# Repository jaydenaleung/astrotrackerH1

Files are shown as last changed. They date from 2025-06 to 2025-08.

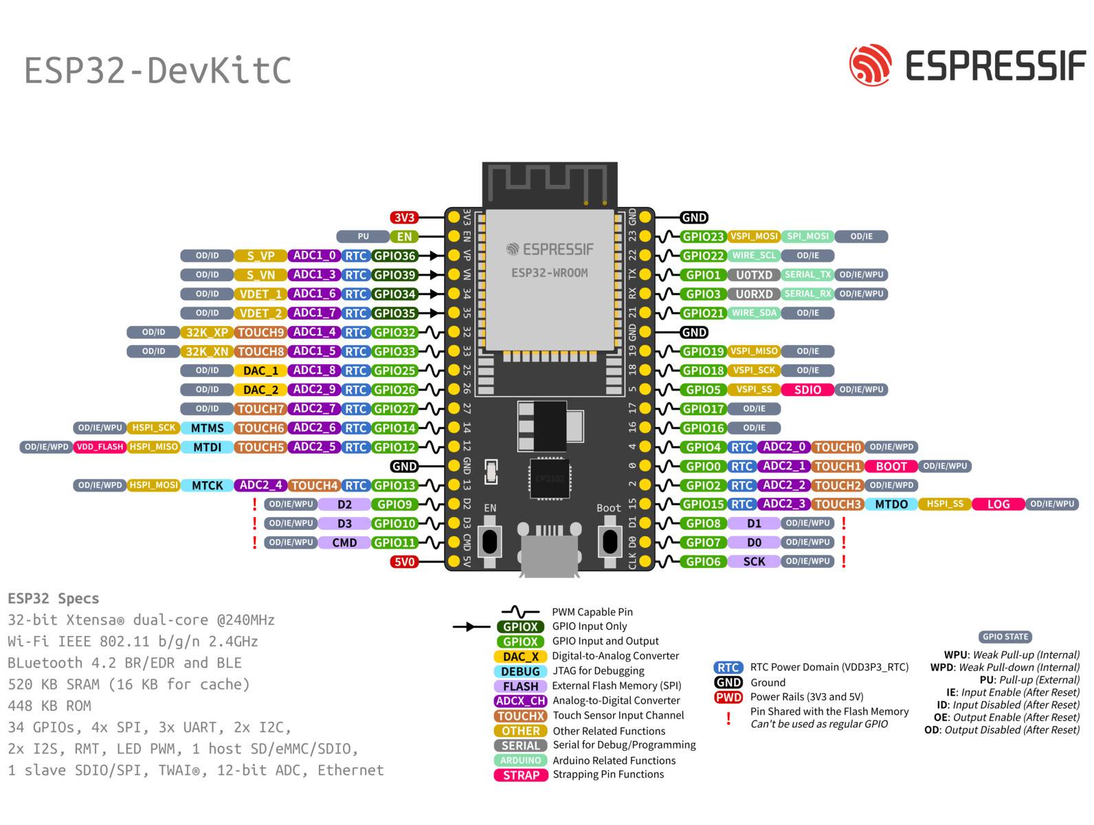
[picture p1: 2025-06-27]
pcb/esp32-pinout.jpg

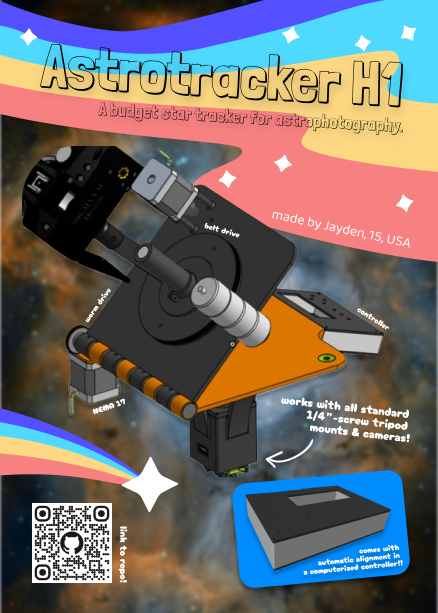
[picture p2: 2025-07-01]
Astrotracker H1 Magazine.png

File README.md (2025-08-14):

# Astrotracker H1
Astrotracker H1 is a DIY star tracker camera mount for astrophotography, made to open access to astrophotography without needing to purchase a more expensive star tracker. Includes a multi-axis rotational gimbal, automatic North Pole alignment, and possible upcoming GoTo integration.

VIDEO DEMO: [https://youtu.be/irbhYrVtJVo](https://youtu.be/irbhYrVtJVo)





# Figures

**Total Minimum Cost:** $220 USD

**Total Hours Spent:** 135 hrs

**Total Days Spent:** 33 days

*See JOURNAL.md and the BOM below for an in-depth explanation of these numbers.*

# How It Works

The Three-Part Process
-

There are always three parts to an engineering project like this, at least for the Highway YSWS program. One is computer-aided design (CAD) modeling; for large projects, this often takes the most time, as it did with this project. Another is printed circuit board (PCB) design, which is the electrical component of the project. Finally, the brain of the build is programmed in the software part, where firmware is written onto a microcontroller that controls the hardware. See the pictures below for how I went about this!

CAD:



PCB:





Firmware:



Star Trackers
-

Since astrophotography is done in very dark environments, a long exposure ranging from a second to the whole night is needed. Due to Earth's rotation, keeping the camera in the same place for a long exposure causes the image to display star trails instead of clear, detailed stars. Star trackers fix this problem by rotating the camera on an equatorial mount aligned with the path of the stars, eliminating star trails. See this picture for a diagrammed explanation:



Astrotracker H1
-

This device attempts to solve these issues by upgrading the traditional equatorial mount to include a polar scope for precise alignment, a counterweight to balance the camera's weight, automatic computerized alignment using azimuthal and latitude (GPS) measurements, and a standard 1/4" tripod mount.

The mechanism is based on two plates connected by a hinge and a rotating gear. The bottom plate is the swivel plate, which swivels 360° and adjusts the azimuthal heading of the device. The other plate is the rotational axis (RA) plate, which tilts to match is angle of elevation to the device's GPS latitude and is driven by a precise worm gear. Matching the device's rotation to face exactly 0° north and its tilt to its GPS latitude allows the RA, the axis perpendicular to and in the middle of the rotating gear and the RA plate, to point exactly to the North Pole (next to the star Polaris). When the RA is pointed toward the North Pole and the rotating gear turns counterclockwise, the tracking will be able to accurately and precisely follow the path of the stars and prevent capturing star trails. Microstepping enhances these features by increasing the precision and resolution of the stepper motor by up to 64 times.



Additional Features
-

Apart from the bare-bones mechanism that drives the star tracker, these upgrades elevate the project to create a truly effective star tracker:
- Automatic, computerized alignment using GPS and compass data
- 1/16 and 1/64 microstepping for stepper motors
- Polar scope for precise adjustment
- Counterweight for balance
- Bubble level for precision
- Thrust and radial ball bearings for smooth rotation
- 12.5:1 reduction ratio for belt-driven rotating gear
- 60:1 reduction ratio for worm gear-driven hinge
- 51:1 reduction ratio for the gearbox on the stepper motor turning the swivel plate
- Organized PCB connecting everything on one board
- Standard 1/4" camera and tripod mount screws
- Ball mount to point camera the right way
- Center control console with up-down-left-right buttons for fine adjustment, start-stop tracking buttons, auto-adjustment capability, and a smart LCD UI interface





# The 'Why' Behind the Project
As an avid photographer and engineer myself, I have always wanted to get more involved with astrophotography. Unfortunately, living in a city didn't play out well for me because of the massive amount of light pollution around me, blocking my view of the stars. I knew I wanted to combine my passions, and the opportunity to do so came through Hack Club's Highway to Undercity program. They fund almost any project you propose to them through their You Ship We Ship (YSWS) initiative.

After conducting some research, I found out that a star tracker was one of the most necessary tools to take better pictures of the night sky. Unfortunately, they were all priced around $500 USD - a hefty investment. Building a star tracker would allow me to combine my passions and achieve a more cost-effective solution at the same time.

# Why This Is Worth Ten Points
This star tracker isn't just any star tracker or equatorial mount - it adds many more complex features that empower young photographers on a budget, like myself, to pursue astrophotography. Fundamentally, the project is already as mechanically complex as a six-point project without all of the additional features. The time spent building intricate features into the mechanical model, custom footprints into the PCB, and special features into the firmware truly takes this project above and beyond the guidelines for a six-point project. 

Not only did I pay attention to the detail and precision needed for such a device with the bubble level, high reduction ratios, and microstepping, but I also considered what would take this above its minimum viable product by adding complex logic for auto-alignment, a balancing counterweight to increase control, and an intuitive LCD user interface controlled with standard pushbuttons. Being able to connect all the electrical components on a single, thought-out PCB and the firmware logic for tracking and auto-alignment indeed also makes this project electrically and computationally complex. Furthermore, I was able to achieve all of these features for under $300 USD when most market star trackers cost about $500 USD. Finally, I spent a ton of time perfecting every detail and feature, putting in almost sixty hours *before* building it (while the recommended minimum time spent for a ten-point project is fifty hours).

# **Bill of Materials (BOM):**

*Note: I am using Aliexpress for some and Amazon for others. Prices listed below are in USD, per part, and rounded. e.g. 2x Nema 17 ($14) = $28 total. Also see the .csv file for the official BOM.*

| Quantity | Name | Price Per Part | Link |
| ----- | --- | --- | --- |
| 2x | Nema 17 stepper motor (regular) | $14 | [https://www.amazon.com/STEPPERONLINE-Stepper-Bipolar-Connector-compatible/dp/B00PNEQKC0](url) |
| 1x | Nema 17 stepper motor (w/gearbox) | $42 | [https://www.amazon.com/51-Planetary-Gearbox-Stepper-Precision/dp/B00QEVLDVO](url) |
| 1x | F8-22M thrust ball bearing | $1 | [https://www.aliexpress.us/item/3256807051413217.html](url) |
| 1x | 10-pack radial ball bearing, 3mm bore | $2 | [https://www.aliexpress.us/item/3256807605344885.html](url) |
| 1x | Worm gear set (worm + gear) | $12 | [https://www.amazon.com/uxcell-Worm-Gear-Set-Reduction/dp/B0DFCVKXLX](url) |
| 1x | PCB board (through JLCPCB & Hack Club $20 Coupon) | $0, covered by coupon | See gerbers.zip in 'pcb' folder |
| 1x | 20-pack 6x6x14 pushbutton | $1 | [https://www.aliexpress.us/item/2255800980685095.html](url) |
| 1x | I2C 16x2 LCD with I2C backpack, blue color | $1 | [https://www.aliexpress.us/item/3256808568663888.html](url) |
| 1x | ESP32 DEVKIT WROOM-32 38-Pin Development Board Type-C | $1 | [https://www.aliexpress.us/item/3256808295104972.html](url) |
| 1x | Resistor pack | $5 | [https://www.amazon.com/Resistor-Resistors-Assortment-Breadboard-Electronics/dp/B0F4P352BB](url) |
| 1x | NEO-8M GPS Module | $1 | [https://www.aliexpress.us/item/3256806859439052.html](url) |
| 1x | QMC5883L Compass Module | $2 | [https://www.aliexpress.us/item/3256807913730129.html](url) |
| 3x | TMC2209 stepper motor driver | $1 | [https://www.aliexpress.us/item/3256808046478114.html](url) |
| 1x | 16T 5mm bore gear | $7 | [https://www.amazon.com/WINSINN-Aluminum-Synchronous-Timing-Printer/dp/B077GMR328](url) |
| 1x | 16T toothless idler bearing for 6mm width GT2 belt, 3mm bore | $9 | [https://www.amazon.com/WINSINN-Aluminum-Timing-Toothless-Printer/dp/B07BPHPYTN?th=1](url) |
| 1x | 2-pack GT2 6mm width belt, 530mm length | $7 | [https://www.aliexpress.us/item/3256808983126633.html?gatewayAdapt=glo2usa4itemAdapt](url) |
| 1x | Polar scope | $27 | [https://www.amazon.com/Tydeux-Polar-Telescope-Finderscope-EQ-5/dp/B0D2L11C4G/](url) |
| 1x | 3-pack 1/4" camera screw | $1 | [https://www.aliexpress.us/item/3256806761503223.html](url) |
| 1x | Camera ball joint mount, red color | $1 | [https://www.aliexpress.us/item/3256802805830814.html](url) |
| 1x | 5-pack bubble level, 18x9mm | $1 | [https://www.aliexpress.us/item/3256808611329580.html](url) |
| 4x | 200g counterweight | $1 | [https://www.aliexpress.us/item/3256807217165073.html](url) |
| 1x | 6S LiPo battery, 22.2V 1000mAh 100C, XT60 connector | $15 | [https://www.amazon.com/Ovonic-Battery-1000mAh-Connector-CINEWHOOP/dp/B07JPK99D9](url) |
| 1x | XT60 male and female plug pack wires, 14 AWG, 15cm length | $1 | [https://www.aliexpress.us/item/3256808104814371.html](url) |
| 1x | LiPo battery charger | $30 | [https://www.amazon.com/B6-Battery-Charger-Discharger-Connectors/dp/B0F2H3XR6S](url) |
| 1x | M4 nuts and bolts, 270 pcs | $9 | [https://www.amazon.com/Kadrick-Assortment-Metric-Washers-Upgrade/dp/B0BZ6XG8PT?th=1](url) |
| 4x | M3 50pcs bolts, 6mm, 12mm, 16mm, 35mm versions | $1 | [https://www.aliexpress.us/item/2255800794906149.html](url) |
| 1x | M3 50 pcs hex nuts | $1 | [https://www.aliexpress.us/item/3256807407546447.html](url) |
| 1x | M2.5x30mm 50pcs bolts | $1 | [https://www.aliexpress.us/item/2255799955713291.html](url) |
| 1x | M2.5 50 pcs nuts | $1 | [https://www.aliexpress.us/item/3256807407546447.html](url) |
| 1x | Allen key set | $1 | [https://www.aliexpress.us/item/3256807283413035.html](url) |
| 1x | Long-nosed plier | $1 | [https://www.aliexpress.us/item/3256805792649837.html](url) |

| **Total minimum cost** | $220 |
| --- | ----- |
| **Total including 'in-case' of price changes, spare parts, etc.** | ~$235 |
| **Total including in-cases, sales tax (assumed ~6%), import and customs fees, etc.** | ~$270 |

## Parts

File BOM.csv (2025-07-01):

Quantity | Name | Price Per Part | Link
2x | Nema 17 stepper motor (regular) | $14 | https://www.amazon.com/STEPPERONLINE-Stepper-Bipolar-Connector-compatible/dp/B00PNEQKC0
1x | Nema 17 stepper motor (w/gearbox) | $42 | https://www.amazon.com/51-Planetary-Gearbox-Stepper-Precision/dp/B00QEVLDVO
1x | F8-22M thrust ball bearing | $1 | https://www.aliexpress.us/item/3256807051413217.html
1x | 10-pack radial ball bearing 3mm bore | $2 | https://www.aliexpress.us/item/3256807605344885.html
1x | Worm gear set (worm + gear) | $12 | https://www.amazon.com/uxcell-Worm-Gear-Set-Reduction/dp/B0DFCVKXLX
1x | PCB board (through JLCPCB & Hack Club $20 Coupon) | $0 - covered by coupon | See gerbers.zip in 'pcb' folder
1x | 20-pack 6x6x14 pushbutton | $1 | https://www.aliexpress.us/item/2255800980685095.html
1x | I2C 16x2 LCD with I2C backpack blue color | $1 | https://www.aliexpress.us/item/3256808568663888.html
1x | ESP32 DEVKIT WROOM-32 38-Pin Development Board Type-C | $1 | https://www.aliexpress.us/item/3256808295104972.html
1x | Resistor pack | $5 | https://www.amazon.com/Resistor-Resistors-Assortment-Breadboard-Electronics/dp/B0F4P352BB
1x | NEO-8M GPS Module | $1 | https://www.aliexpress.us/item/3256806859439052.html
1x | QMC5883L Compass Module | $2 | https://www.aliexpress.us/item/3256807913730129.html
3x | TMC2209 stepper motor driver | $1 | https://www.aliexpress.us/item/3256808046478114.html
1x | 16T 5mm bore gear | $7 | https://www.amazon.com/WINSINN-Aluminum-Synchronous-Timing-Printer/dp/B077GMR328
1x | 16T toothless idler bearing for 6mm width GT2 belt 3mm bore | $9 | https://www.amazon.com/WINSINN-Aluminum-Timing-Toothless-Printer/dp/B07BPHPYTN?th=1
1x | 2-pack GT2 6mm width belt 530mm length | $7 | https://www.aliexpress.us/item/3256808983126633.html?gatewayAdapt=glo2usa4itemAdapt
1x | Polar scope | $27 | https://www.amazon.com/Tydeux-Polar-Telescope-Finderscope-EQ-5/dp/B0D2L11C4G/
1x | 3-pack 1/4 inch camera screw | $1 | https://www.aliexpress.us/item/3256806761503223.html
1x | Camera ball joint mount red color | $1 | https://www.aliexpress.us/item/3256802805830814.html
1x | 5-pack bubble level 18x9mm | $1 | https://www.aliexpress.us/item/3256808611329580.html
4x | 200g counterweight | $1 | https://www.aliexpress.us/item/3256807217165073.html
1x | 6S LiPo battery 22.2V 1000mAh 100C XT60 connector | $15 | https://www.amazon.com/Ovonic-Battery-1000mAh-Connector-CINEWHOOP/dp/B07JPK99D9
1x | XT60 male and female plug pack wires 14 AWG 15cm length | $1 | https://www.aliexpress.us/item/3256808104814371.html
1x | LiPo battery charger | $30 | https://www.amazon.com/B6-Battery-Charger-Discharger-Connectors/dp/B0F2H3XR6S
1x | M4 nuts and bolts 270 pcs | $9 | https://www.amazon.com/Kadrick-Assortment-Metric-Washers-Upgrade/dp/B0BZ6XG8PT?th=1
4x | M3 50pcs bolts 6mm 12mm 16mm 35mm versions | $1 | https://www.aliexpress.us/item/2255800794906149.html
1x | M3 50 pcs hex nuts | $1 | https://www.aliexpress.us/item/3256807407546447.html
1x | M2.5x30mm 50pcs bolts | $1 | https://www.aliexpress.us/item/2255799955713291.html
1x | M2.5 50 pcs nuts | $1 | https://www.aliexpress.us/item/3256807407546447.html
1x | Allen key set | $1 | https://www.aliexpress.us/item/3256807283413035.html
1x | Long-nosed plier | $1 | https://www.aliexpress.us/item/3256805792649837.html
Total minimum cost | $220
Total including 'in-case' of price changes; spare parts; etc. | ~$235
Total including in-cases; sales tax (assumed ~6%); import and customs fees; etc. | ~$270

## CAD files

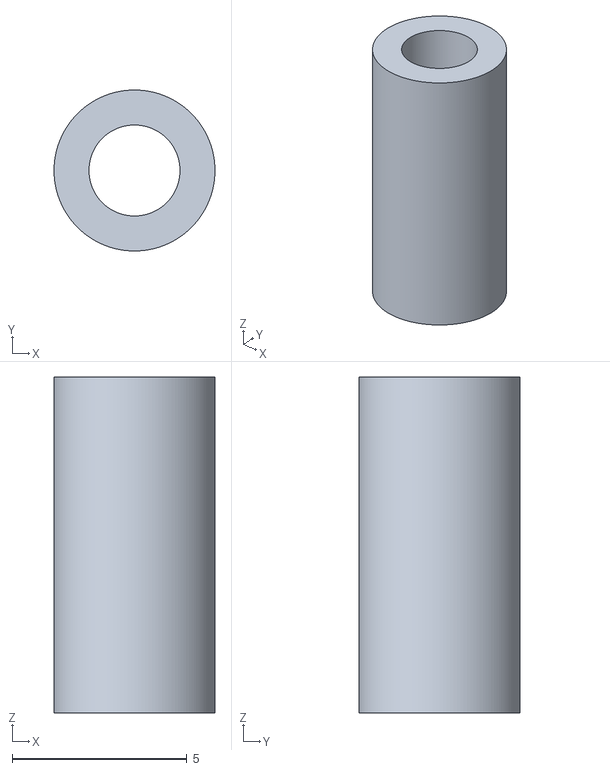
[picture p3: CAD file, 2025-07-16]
cad/parts to print/M2.5x9.6mm spacer - Part 1.stl
4.60 x 4.60 x 9.60

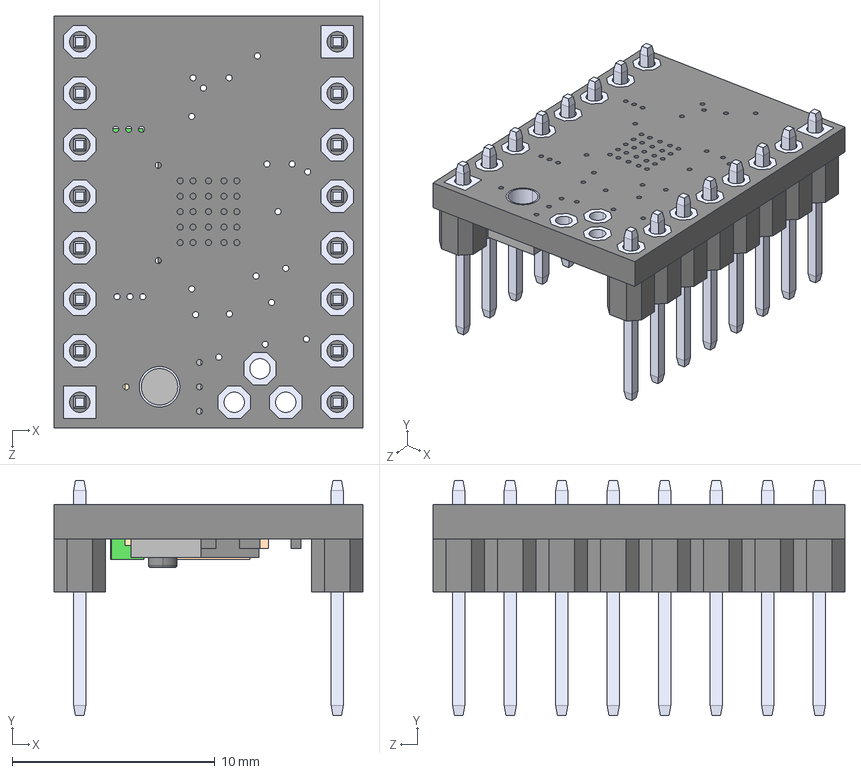
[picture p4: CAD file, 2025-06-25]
cad/reference/TMC2209_SILENTSTEPSTICK.step
15.2 x 11.6 x 20.3 mm

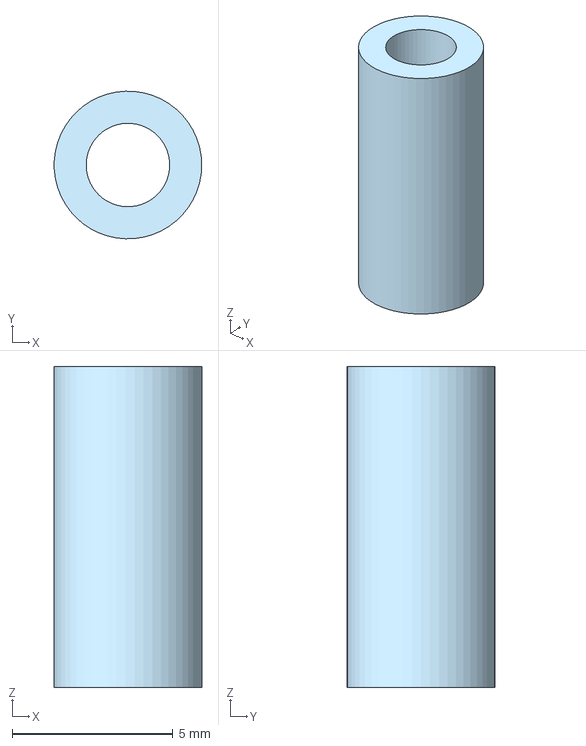
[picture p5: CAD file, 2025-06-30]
cad/spacers/M2.5x10mm spacer.step
4.60 x 4.60 x 10.0 mm

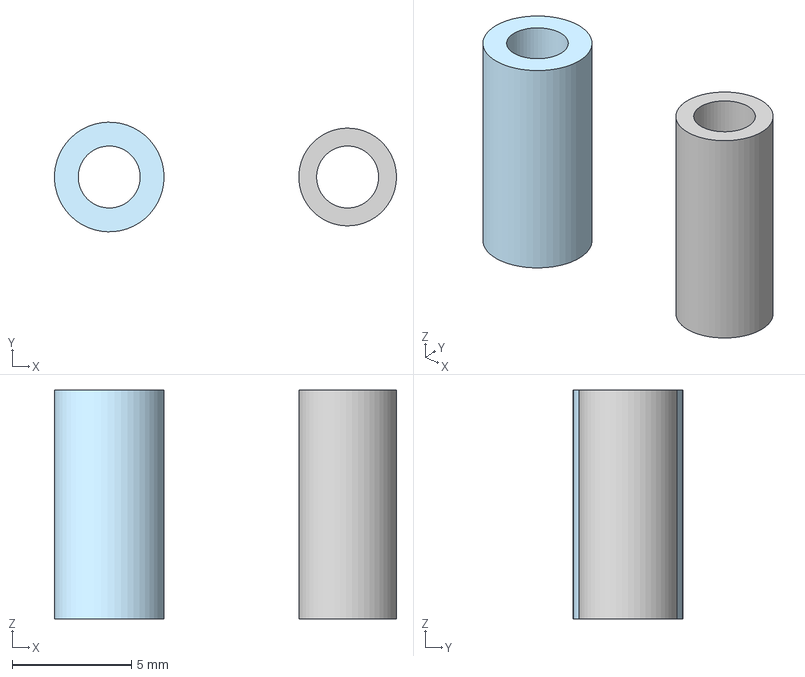
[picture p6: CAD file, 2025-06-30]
cad/spacers/M2.5x9.6mm spacer.step
14.3 x 4.60 x 9.60 mm

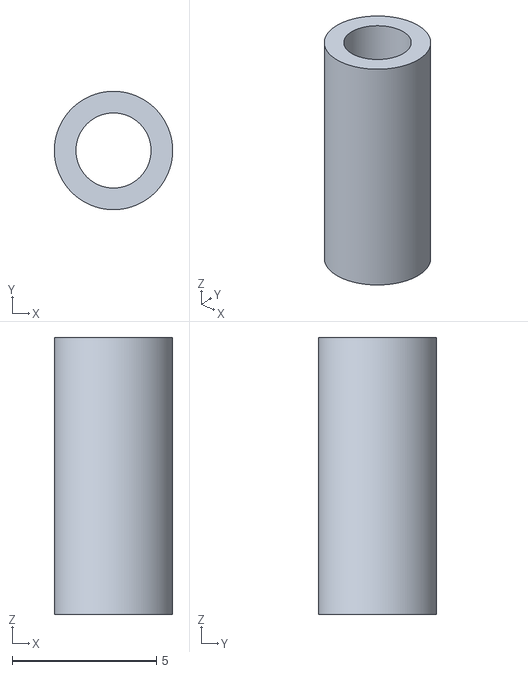
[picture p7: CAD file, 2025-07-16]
cad/parts to print/M2.5x9.6mm spacer - Part 2.stl
4.10 x 4.10 x 9.60

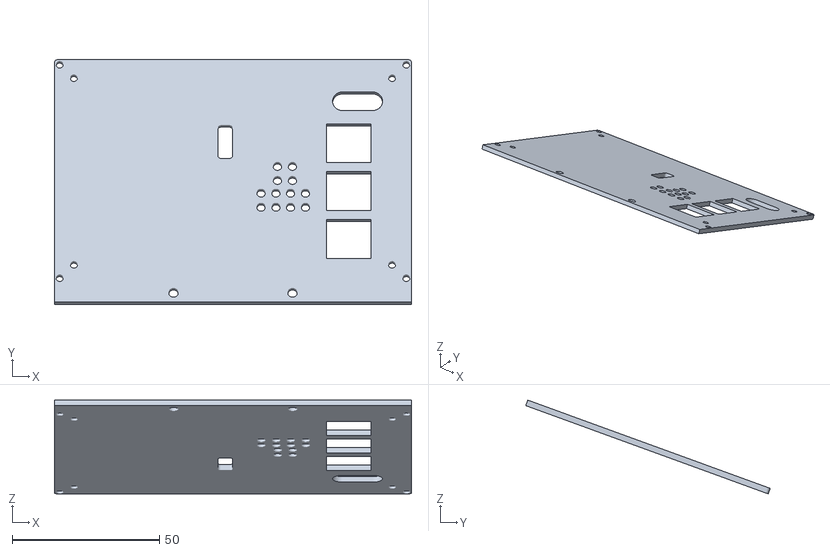
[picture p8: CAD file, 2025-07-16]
cad/parts to print/Swivel Plate - Part 1.stl
121.3 x 83.1 x 31.9

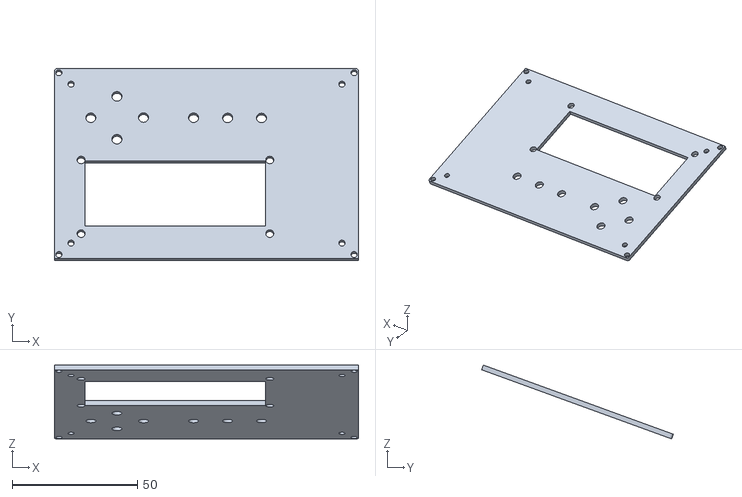
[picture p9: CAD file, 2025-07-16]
cad/parts to print/Swivel Plate - Part 4.stl
121.3 x 76.5 x 29.5

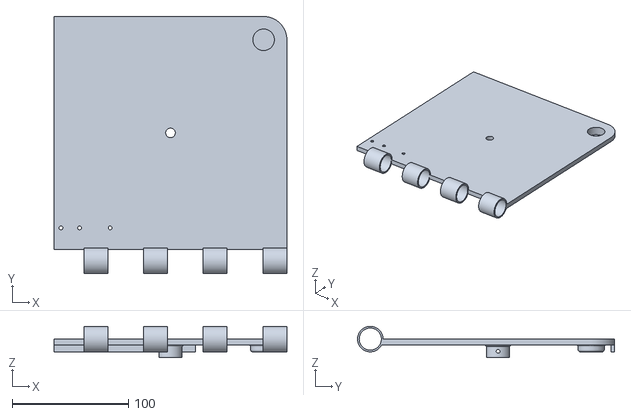
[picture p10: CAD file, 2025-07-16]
cad/parts to print/Swivel Plate - Part 7.stl
200.0 x 220.8 x 27.0

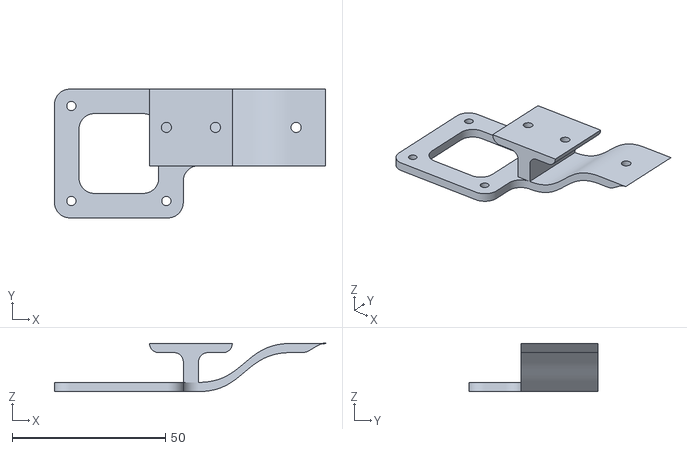
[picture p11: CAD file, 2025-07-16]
cad/parts to print/Swivel Plate - Part 6.stl
88.4 x 42.0 x 15.7

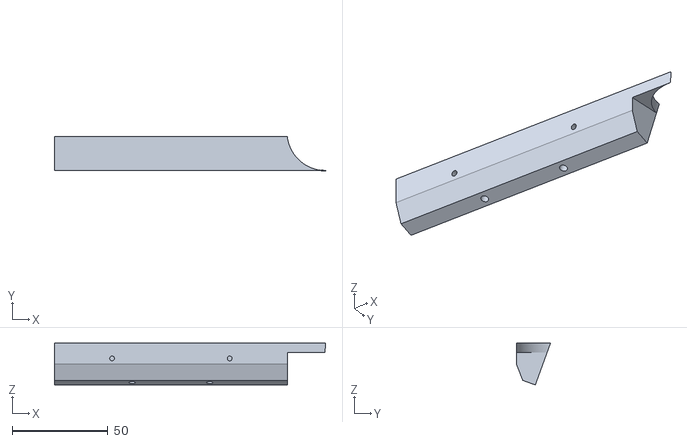
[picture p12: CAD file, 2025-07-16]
cad/parts to print/Swivel Plate - Part 8.stl
141.2 x 17.8 x 21.8

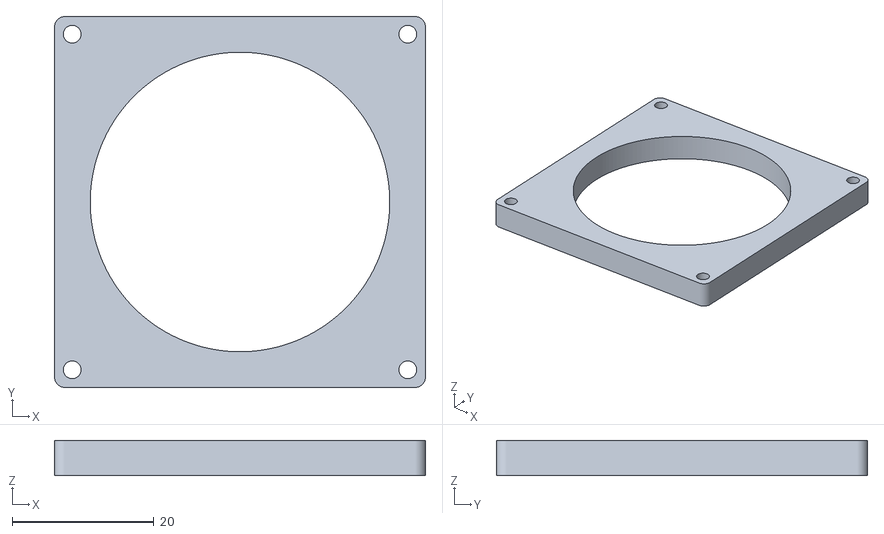
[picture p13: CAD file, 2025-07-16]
cad/parts to print/swivel motor housing - Part 1.stl
52.4 x 52.4 x 5.00

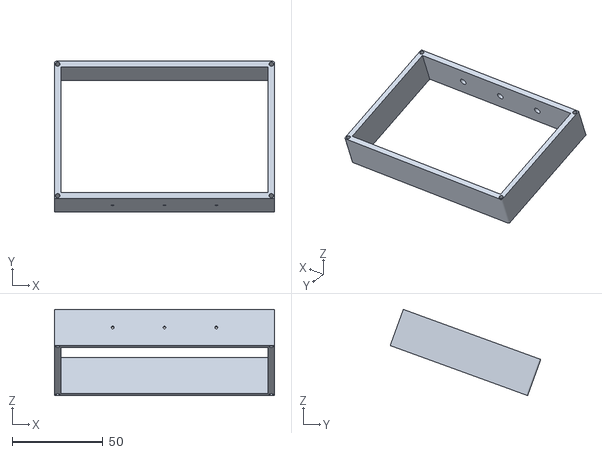
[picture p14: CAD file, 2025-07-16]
cad/parts to print/Swivel Plate - Part 3.stl
121.3 x 83.1 x 47.5

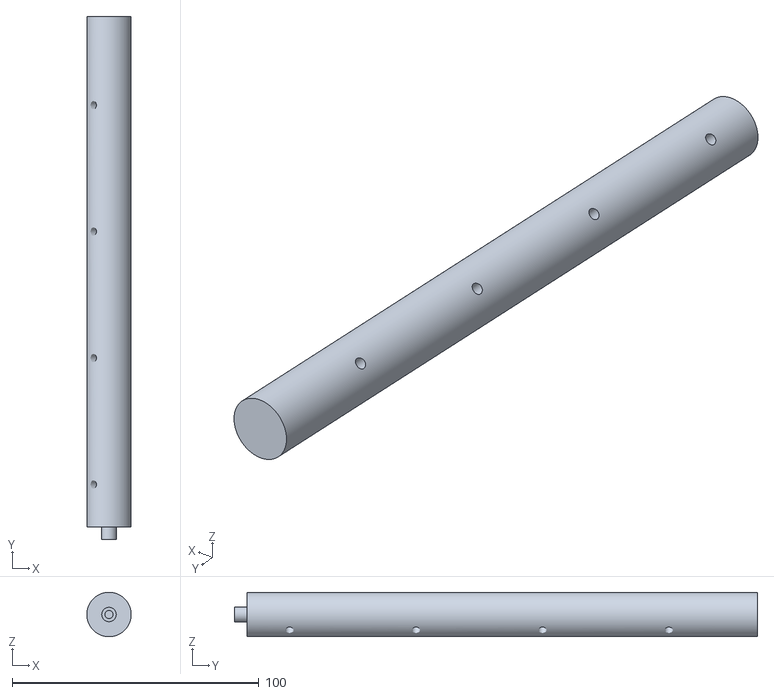
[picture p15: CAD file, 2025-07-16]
cad/parts to print/hinge - Part 1.stl
18.0 x 212.0 x 18.0

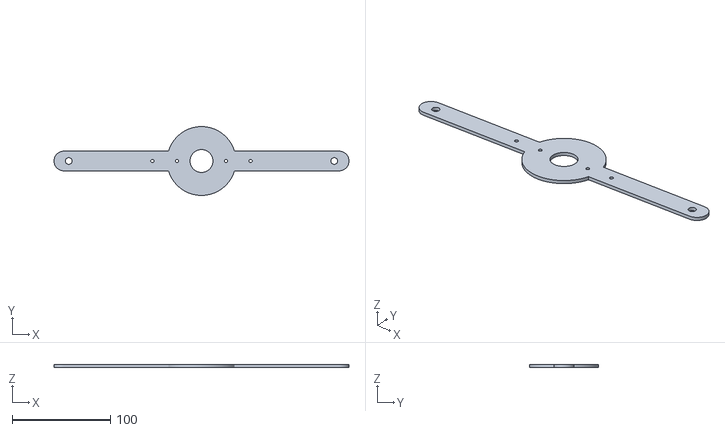
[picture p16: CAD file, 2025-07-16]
cad/parts to print/camera mount - Part 1.stl
300.0 x 70.0 x 3.00

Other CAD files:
cad/parts to print/M2.5x10mm spacer.stl
cad/parts to print/RA Plate - Part 1.stl
cad/parts to print/polar scope circlip - Part 1.stl
cad/parts to print/M4x0.8mm spacer.stl
cad/parts to print/M3x8mm spacer.stl
cad/spacers/M3x8mm spacer.step
cad/spacers/M4x0.8mm spacer.step

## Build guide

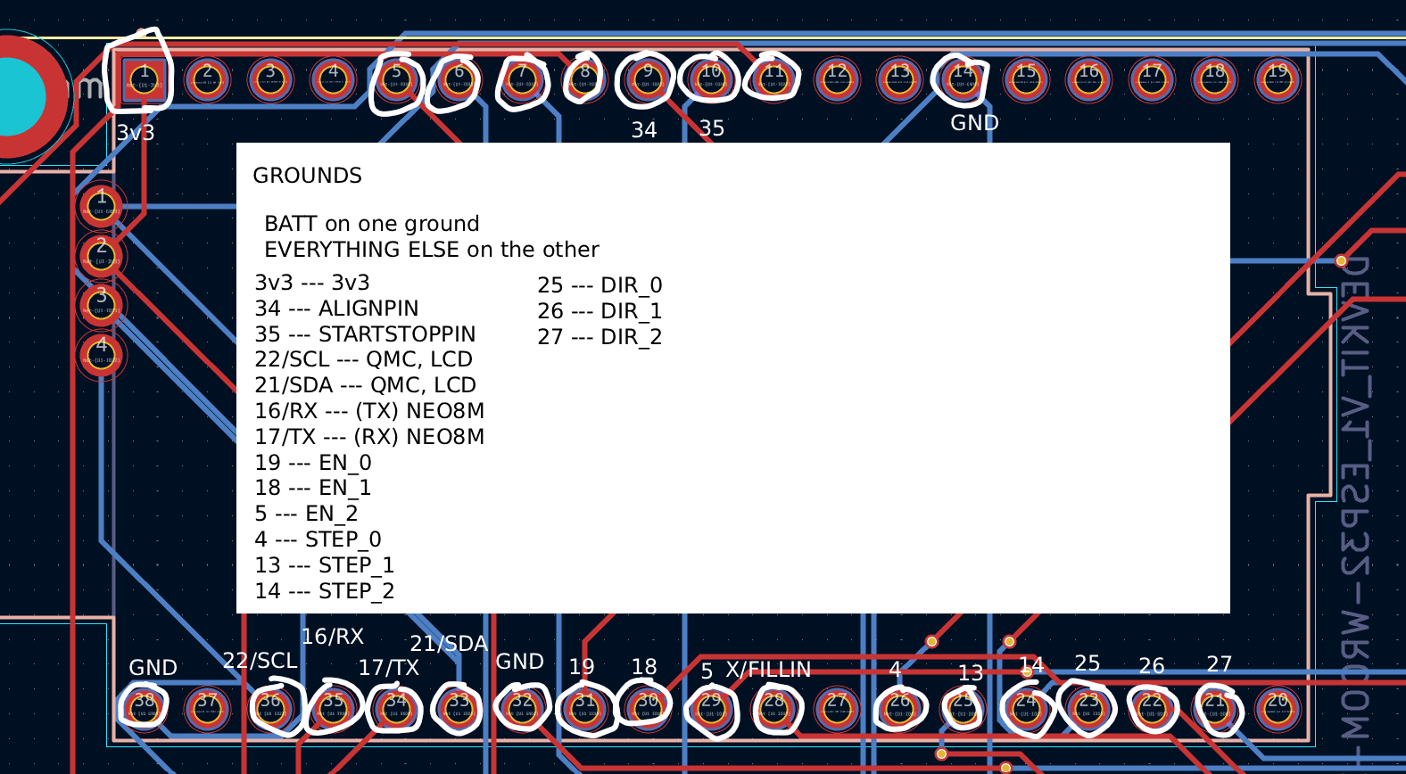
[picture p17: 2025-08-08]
pcb/ESP32 30-Pin Wiring Diagram Translation.png

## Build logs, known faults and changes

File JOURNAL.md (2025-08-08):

---
title: "Astrotracker H1"
author: "Jayden Leung (Hack Club Slack: loliipoppi)"
description: "DIY star tracker for astrophotography with a 360° azimuthal axis, adjustable tilt, and automatic North Pole finding."
created_at: "2025-06-11"
---

# Time Spent
- **Total hours: 135h**
- **Total days: 33 days**
- **Time spent on CAD: 27.5h**
- **Time spent on PCB design: 11h**
- **Time spent on coding: 9h**
- **Time spent on physical assembly: 78h**
- **Time spent on sourcing parts, writing journal and readme, etc.: ~10.5h**

# June 11th: Research and Planning

Before beginning the technical work on my project, I needed to first research how a star tracker worked and what the best design for it was. I learned my lesson in previous projects to do this step first before jumping right in so I can maximize my efficiency. Bottom line, start with your MVP (minimum viable product) and build up instead of shooting for the stars and having to cut down on your project.

ChatGPT was my best friend here. I looked at a few YouTube videos, websites, forums, similar projects, etc., but ChatGPT was able to answer all my questions on simple star movements. Here are some of the resources I used: https://wiki.openastrotech.com/en/OpenAstroTracker, https://openastrotech.com/, https://agenaastro.com/sky-watcher-star-adventurer-gti-goto-mount-head-kit-s20590.html?rfsn=7382628.cf60d1, https://www.youtube.com/watch?v=RtHJ5TVkeu4

Through a series of questions, conclusions, and deductions (see my whiteboard planning below), I found out that, from Earth, stars appear to move east/counterclockwise around Polaris (the north star) at the sidereal rate (~15°/hr). This meant that all I had to do was point the axis of my rotational plate towards Polaris and turn the plate counterclockwise at 15°/hr to match the movement of the stars. It also turned out that this would work no matter the direction the camera was pointed in or even if the camera wasn't centered on the rotational axis, as long as it was physically connected to the rotational plate.



I also sketched a few examples of what the tracker could look like in CAD. I eventually settled on the second iteration (look at the second picture). Sketching first helped me to effectively iterate and create the most efficient design without having to take a lot of time.




This was my MVP in the end (see below). There were a few assumptions and oversights that I intentionally made to simplify the design first.

Functions (Must be able to…):
- Rotate the rotating base
- Have near-270 deg turn for camera
- Align the rotating base

Parts (Must have…):
- Base that rotates the rotating base
- Rotating base - stepper motor
- Mount on rotating base for camera (use tripod mount on the camera)

Restrictions (OK to not have…):
- Belt drive/worm gear & ball bearings
- Tripod mount
- Northern/southern hemisphere switching
- Auto Correction for Polaris/rotating base calibration depending on coords
- GoTo compatibility
- Offset for through-hole polar scope OR polar scope off to the side

**Total time spent: 5h**

# June 12-13th: CADing the Rotational Plate and Hinge

The next two days after planning I spent CADing the rotational plate, swivel plate, and the hinge that connected them in Onshape. I followed the format shown in the second design (look at the previous journal entry). I decided to have the rotational gear (RA gear) be connected to a stepper motor through a belt drive system. This would provide enough torque to move the heavy camera and enable the device to rotate the plate at the slow speed of 15°/hr. I first settled for a 400T RA gear, which would give me a 1:25 gear ratio for a 16T stepper motor gear. With 1.8° steps and 1/32 microstepping (using PWM to split the steps even further on the stepper motor), that would have given me about 8.1 arcseconds/microstep, which was within the optimal range for medium to long range (zoom) astrophotography.

After discovering that a 400T gear was pretty big, I settled for a 200T gear instead but had to increase the 1/32 microstepping to 1/64 to maintain the rotational rate of 8.1 arcsecs/microstep. This would also give me enough torque to move a payload of about 500g-1kg. I ran some calculations and found that the optimal center to center distance between the RA gear and the stepper motor gear was 100mm. This would allow the gears to be close enough to mimize the size of the plate while still allowing enough space between the two gears for idler bearings that would fit the timing belt tighter. 200T gear, 16T gear, and 100mm C-C dist => 530mm GT2 belt; the GT2 belt had a pitch (tooth-to-tooth distance) of 2mm and was a bit long for the setup, but was perfect after securing it with a 20T toothless idler bearing that jutted 3.1mm into the belt.

I CADed this onto the rotational plate (RA plate), which I then connected via a hinge controlled by a worm gear to the swivel plate. The swivel plate would allow the whole mechanism to swivel along the azimuth/horizon, and the worm gear tilted the RA plate towards Polaris (the angle of elevation of the plate should equal my GPS latitude). The RA gear was generated by an Onshape script, and I CADed its additional details by hand since I couldn't find an internet model for a 200T belt drive gear. I found one for the 16T gear, though. See the picture below!

Screenshot 2025-06-16 at 3 56 46 PM

**Total time spent: 5.5h**

# June 16th: CADing the Swivel Plate and Adding Accurate Part Models

I spent today adding the functionality for the swivel plate (the plate that is connected to the RA plate by a hinge) by creating a housing for another NEMA 17 stepper motor with a 51:1 gear reduction gearbox. On top of the motor sits a thrust ball bearing, and on top of that sits the swivel plate and the entire mechanism with it. Next time, when I put the finishing touches on my CAD model, I'll make sure to add arms to the housing that curve up to support the heavy swivel plate; I didn't get to do it this time. This is a crucial part of the device since it rotates the RA plate to face Polaris on the azimuthal axis. However, I do have some reservations about allowing the entire mechanism (possibly ~500g) to sit on top of a ball bearing and a motor housing, especially when considering the extra 1-2kg load put on by the camera and its opposing counterweight. Those changes will have to be determined after printing and testing.

In case you're confused about how I spent five hours on this, I had to first research the best way to effectively rotate the swivel plate, run calculations to find the best motor gearbox that would allow for enough torque, and find the best bearing that would work for this. I also finally decided to spend some time finding online models of the motors and bearings I was using. To my great surprise, downloading the files as STEP files instead of STL files made it SO MUCH EASIER because I was working with solid, editable parts rather than meshes. Onshape was much friendlier to me with these files because of this. I was surprised because I thought I had tried this before with an earlier plane project, and they still were meshes. Meshes or not, this greatly simplified my work as it allowed me to make the right edits to these models to ensure they were accurate to the specific motor dimensions I was working with.

For reference, here are some great websites and libraries of CAD models that were helpfuL: [https://grabcad.com/library](url), [www.traceparts.com/en](url), [https://www.thingiverse.com/](url), (next two are more STLs and 3D printing files, along with Thingiverse) [https://cults3d.com/](url), [https://www.printables.com/](url).

And just as a side note, before I started working on the CAD files, I finally decided to make and update my journal. It took a few hours since I re-read all the custom project rules and had to set up my journal from scratch.

Pictures of the updated assembly!
Screenshot 2025-06-17 at 5 20 49 AM
Screenshot 2025-06-17 at 5 21 13 AM
Screenshot 2025-06-17 at 5 21 43 AM
Screenshot 2025-06-17 at 5 22 08 AM

**Total time spent: 5h**

# June 18-23: Finishing the CAD (for now)

Throughout these six days (I was working quite sporadically, which is why it took so long), I finally finished adding the final touches and reference model to my assembly. It looks great!! I employed a dark grey-orange color scheme to match the color of my tripod.

Before I reveal the final result, I'll list the changes I made:
- Added real models of the NEMA 17 stepper motors
- Created and added housing for the NEMA 17 gearbox that turns the whole mechanism
- Implemented a thrust bearing to make the turning of the mechanism smoother
- Added arms onto the motor housing to better support the heavy mechanism, using ball bearings to reduce friction
- Added compatibility for the polar scope
- Added a mount for the camera and its counterweight
- Added a restraining clip to hold the gear and camera mount down
- Added a bubble/spirit level on the swivel plate for extra accuracy
- Placed ball bearing model into the assembly
- Placed polar scope model into the assembly
- Placed camera, camera mount, counterweight, and 1/4-20 screws for the camera into the assembly
- Placed tripod into the assembly
- Changed colors to dark grey-orange to reflect my tripod
Screenshot 2025-06-23 at 8 30 47 PM

Here are the final results! I'll update the model again after I'm finished with the PCB design, and I'll add a housing for the PCB.
Screenshot 2025-06-23 at 8 30 19 PM
Screenshot 2025-06-23 at 8 30 32 PM
Screenshot 2025-06-23 at 7 49 47 PM

**Total time spent: 9h**

# June 24: PCB Part Sourcing & Schematic

As I got started on my PCB design (which, as I found being a beginner, had a steep learning curve), I quickly ran into trouble sourcing parts, symbols, footprints, and the like. I found [snapeda.com](url) (and surprisingly, no other websites) to be really helpful in this, until I encountered the "No 2D model" (symbol or footprint) label for some parts. These were mostly the parts that weren't as common, such as the QMC5883L compass module I was using, so I had to learn how to make the footprints and symbols by hand. While it was certainly frustrating and time-consuming, I think it was a good exercise, as I heard from people around the internet that that was a common area of PCB design. Here's a good resource I found: [https://www.youtube.com/watch?v=NiSkKemLK_8](url). I had to make "empirical measurements," which really involved me putting a clear, plastic ruler to my computer screen to measure my parts for my custom footprints. Fortunately, I don't think they were too inaccurate, but I'd have to check that when my PCB is delivered.

Because of the reasons mentioned above, I think that the PCB design step was the hardest (at least so far). Surprisingly, it took only half the time as to do CAD, which I was already pretty proficient in. I certainly learned a lot. For example, someone on the Hack Club Slack told me I could just use net flags instead of a ton of wires. Also, (about) seven and a half hours! It was certainly a sprint... but Undercity is a marathon! (get it, because it's a hackathon... haha...)

Here's the schematic:


Here's a custom footprint I made:


**Total time spent: 7.5h**

# June 25: Routing & Finishing the PCB

To be honest, I thought routing the board would be a pain because of the immense number of wires I placed down in the schematic. It was actually pretty chill... except for the insane amount of vias I placed down (4+ vias on one connection??). However, it still stands now as one of my favorite parts of the engineering process. It's very satisfying to route the PCB and see your work come to life; in fact, seeing the fruits of my efforts so quickly is one of the primary reasons I do engineering in the first place.

It wasn't without some effort, however. I had to fix a few things on the schematic that the DRC picked up (pin numbers, annotations, file changes, etc.), as well as place the footprints in the right place. I spent a good amount of time trying to figure out how to put certain footprints on the back, only to find out you just have to press 'F'. I wanted to place them on the back so I could have the LCD screen and buttons in the front and all the microcontrollers/logic/drivers/etc. out of the way. It did come with the nice benefit of being able to place the footprints on top of each other to save space (given that the through-holes don't touch). After adjusting the Edge.cuts rectangle to extend 3mm from the outmost point on each side, I began routing.

Here's my finished PCB layout, before routing:


And after:


**Total time spent: 3.5h**

# June 25-27: Coding the Firmware

After finishing my PCB on June 25th, I moved on to the software piece. I really had no idea what to expect from this phase since I've had relatively little experience programming hardware. Funny enough, although I had a bunch of components and functionalities as well as almost 500 lines of code, it took me the least amount of time compared to the other areas of this project.

I coded for the ESP32 in the Arduino IDE. I started with the stepper motor drivers, which I had to consult various website tutorials, official library code on Github, and ChatGPT. I quickly realized the learning curve, but thankfully it didn't take me long to understand the code I needed to write. After really being able to understand and engage with the software, I started to really enjoy the experience! I learned a lot about I2C serial buses, UART communications, and firmware coding. After the stepper drivers, I moved onto the more software-like piece (as opposed to firmware coding) where I programmed the logic for manually adjusting the tilt and azimuth of the mechanism using a set of four up-down-left right buttons. I also implemented another button for auto-North Pole alignment by matching the tilt of the mechanism to my GPS latitude and turning the mechanism to face north (see GPS and compass modules in the next-next sentence). Two more buttons were used for starting and stopping tracking. Then, I moved onto the NEO-8M (GPS) and QMC5883L (compass) modules, which were relatively simple to extract data from to use. Finally - and arguably the most time-consuming and problem solving-intense part - I programmed the UI through an I2C serial bus LCD interface. I had a few screens, which were:
- Home screen: "READY FOR ALIGNMENT"
- Auto-alignment: "ALIGNING + Latitude + Heading / x secs left…"
- Auto-alignment complete: "ALIGN COMPLETE (for 1s)"
- Tracking on: "TRACKING… / x hours x minutes x seconds"
- Tracking off: "STOPPED (for 1s)"
- Manual alignment: Shows custom arrows on the home screen to indicate direction
- Other custom markings/logos for azimuth, latitude, which hemisphere the device is in, etc.

In the process of doing so, I had to implement a few complex features such as tracking elapsed time, saving to non-volatile memory, etc. It was a fun excercise that increased my coding skills!

Examples of my code:
Screenshot 2025-06-28 at 12 08 58 AM
Screenshot 2025-06-28 at 12 08 26 AM
Screenshot 2025-06-28 at 12 09 18 AM

**Total time spent: 9h**

# June 28-30: Preparing to Propose the Project

After finishing the firmware, most of the project was already finished. The only steps left were to add a housing onto the structure for the PCB in CAD, finish sourcing parts and writing my BOM, update my journal and readme, and submit! For the housing, I figured I could just export the PCB from KiCad as a STEP file and make the holes in the case using that solid part. It made it a lot easier, except that I decided to make the housing on a sloped plane, which didn't work well when I tried to align the coordinates of the PCB with my sketch (the coordinates were in the XYZ direction). I began to finish my part sourcing during this stage because I needed the dimensions of the electronic components I was using to make the housing. This was also helpful because I realized that I needed to make two more holes for my LiPo battery supply.

Before submitting, I read over the submission guidelines again to make sure I had what I needed. Then, I went to write my journal (which I'm doing now!), and after this, I will write the readme and submit. Even though I still have a ways to go until the project is built and finished, I have to say that this project (50+ hours!) is one of the biggest projects I've ever built, one of the projects I'm most proud of, and definitely the project where I've learned the most. I first-handly experienced the learning curve at the beginning of a stage - whether it be CAD, PCB, or software - and saw how easily I could beat it if only I persevered through the beginning, explored, and put lots of time into it. In fact, my favorite outcome from this project isn't the final product but all of the skills I picked up through the way and the fun of learning so quickly. Thank you, Hack Club, for making this YSWS and community possible - I've been absolutely obsessed with Highway to Undercity for the past few weeks.

The BOM can be found in the readme. Of course, some pictures of the final design (CAD, PCB, and my magazine page design):
Astrotracker H1 Magazine


















You can never have too many pictures!

**Total time spent: 12h**

# July 18-20: Printing

Today is printing day! Preparing the models took about an hour, but nothing compared to the time it took to print them - about fifty hours. My poor 3D printer :( but I recieved the black and orange filament, which made for some sick colors. I previously had some bed adhesion issues with my Elegoo Neptune 4 Pro, but I figured out that I could fix them by washing the plate with hot water each time, then reapplying glue onto the buildplate where it would print. That, and lowering the print speed to avoid layer shifting. I think I went through three glue sticks...

**Total time spent: 2h** (preparing models and cleaning print beds)

# July 21-25: Putting The Model Together & Testing Connections

During this time, I tried to put the model together as best as possible. I began with the two plates and, realizing they needed a bit more attention, turned my focus to the motors instead. The housing I made for one of the motors was too small, so that was a pain to manually scrape out (I didn't want to print another one). Similar labor followed.

As for the electrical aspect, I began by soldering everything I could onto the PCB. Bad idea. I thought this would help since I could just complete the PCB and forget about the electrical, but woah... was I wrong. Later, I ended up taking out everything I put onto the PCB and testing them each individually by hand before placing them again on the PCB.

**Total time spent: 12h**

# July 26th: Electronic Prototyping

Today I set out to prototype my circuits, and I began by soldering additional header pins onto my already-soldered header pins. This would allow me to also be able to use jumper wires to prototype on a breadboard before laying it in stone on a PCB. However, I quickly ran into problems. After wiring a stepper motor, an ESP32, and a driver, I forgot to ground the ESP32. When I plugged my 6S LiPo battery (not for the first time, this was a later time), I heard a pretty loud spark (did I just fry my driver...)? Moreover, the ESP32 I bought from Aliexpress didn't have an auto-reset circuit, so it took me an hour to figure out that I had to manually short the GPIO0 pin to ground to force it into bootloader mode (since it wouldn't do it automatically) and that it turned out that I wasn't even plugging in GPIO0 (I had header pins hanging off the side, so I accidentally plugged it into the wrong place). Electronics is very frustrating, but I learned to be more careful.

That said, the circuit didn't work, so something else was probably off. However, I unplugged everything from the ESP32 - which was also unstabily soldered onto the PCB at an angle anyway - to test why it wasn't auto-resetting, so I will leave the rest of the prototyping to another day.

PICTURES

**Total time spent: 6h**

# August 2: Mechanical Part 2

After a brief hiatus to work on my other project, I returned to physically assembling my build. I finished putting the rotational axis (RA) plate, the swivel (base) plate, and the hinge together (with, of course, some handy modifications to the plates and a good amount of hot glue), and I mounted the hinge motora. I finished scraping out the motor housing for the swivel motor (which was still a pain - but heating it up with a heat gun worked). I even mounted my worm and gear, which turned out to be positioned really nicely! Until I screwed it in a bit too much and broke the small part it was screwing onto... hot glue became my friend here.




**Total time spent: 2h**

# August 3-6: Electrical Part 2 - The Good, The Bad, The Ugly

As always, the electrical aspect was a really big pain. But I'm actually really glad for the struggles I went through this time, because the answer wasn't so silly and I learned a lot from it.

I2C LCD:
- Worked normally, but I decided to power it through my 5v power bank instead.
- Seemed to be dim running on 3.3V.

NEO-8M GPS Module:
- Worked at first, but I spent a good amount of time wondering why it wasn't getting any satellite data.
- The reason was because (1) it may have been only showing binary messages, so I wrote a serial command to change it to output NMEA address like it should, or (2) I wasn't outside, or (3) the breadboard connections were pretty loose - once I soldered them, I got solid GPS data.
- Was pretty cool to see it work.

QMC5883L Module:
- Turns out it wasn't really a QMC5883L module - the factory gave me a different chip under the guise of a QMC5883L module to save costs.
- I was getting gibberish because I didn't have the right register addresses.
- The different chip, I found, was a QMC5883**P** chip. I came across this answer in a forum I saw, and the person who discovered that also provided example code and a datasheet. I was very grateful for that.

A4988/TMC2209 Stepper Motor Driver + NEMA 17 Stepper Motor:
- The most difficult piece of hardware I worked with for this project. Sounds really simple, but it wasn't for me.
- A few issues: didn't have a multimeter, the wiring on the Amazon page from the manufacturer was wrong, used a 22.2V (6S) LiPo battery instead of a 12V lead-acid one (my later replacement), made two of my TMC2209s "explode", rendered another TMC2209 and one or two A4988s unusable, accidentally fried my last 38-pin ESP32 by shorting 12V to its ground with the multimeter, A4988 current maximum was too low, and I had limited access to replacement parts.
- My solutions: used A4988s instead of TMC2209s, bought a multimeter and a 12V battery instead of a 6S LiPo, and I finally figured out that my motor was just jittering when I swapped two of my motor coil wires, and suddenly it worked perfectly. I cried in pain for such a simple solution that I'd overlooked many times that had caused me about three consecutive days of consistent trial and error (not to worry, wasn't my fault, the Amazon wiring was wrong and I'd been strictly following that...).
- My lessons: learned a lot about voltage, amperage, batteries, etc. Undercurrent and overvoltage were common issues for me. Also, don't ever trust the manufacturer's color-coded wiring for stepper motors - instead, connect two wires and see if the shaft is harder to turn. If it is, then that's a pair, and you can connect both +/1 or -/2 outputs to it. *Don't overlook anything.* Multimeters are helpful.




P.S. There was this really nice electronics store in Toronto that I got my battery from, and it's literally a hardware hacker's dream. There's like every type of hardware you can imagine... combine that with a Home Depot and you basically get Undercity's hardware shop but at warehouse size.



**Total time spent: 35h** (much better than my last project considering this had more complicated parts!)

# August 7: The PCB, Finally; Mechanical Part 3; and The Final Stretch

10:30 AM. I'd gone to bed late the previous night. A little over thirteen hours until the submission deadline. It was the final stretch. Today, I was able to replicate the success I had the previous night with the motors and turned to testing them all at once. I figured out that I couldn't power all three drivers at once - Vref dipped significantly. However, I found out later that by setting the ENABLE pin high, I could prevent the driver from drawing too much current from the battery so that one driver would be able to draw enough current. After testing each of the motors, I tried to use a multimeter to measure the Vref level of one of the drivers... but accidentally shorted the 12V battery pin to the ground pin, instantly frying my last 38-pin ESP32 (which fit on my PCB). 

Unfortunately, this meant that I had to now "translate" my PCB to a 30-pin ESP32; that is, I soldered jumper wires to the important pins on the PCB, with the other end going to pins on my 30-pin ESP32. That took a while, but after that, I had even more soldering to do. I finally soldered all my other components (including the satisfying line of resistors) - by that time it was about 8:30PM when I finished soldering, and after dinner, I turned to combining the electrical with the mechanical.

I finished the mechanical piece by adding some rubber bands and springs to my hinge so that the worm and gear would mate better, mounting the jerry-rigged PCB housing onto the swivel plate, placing the cap on the swivel motor housing, attaching all my motors, and finally placing my camera and its counterweight on it.

The hinge motor didn't worked as well as I wanted it to since it kept pushing the gear up instead of rotating it. However, when I applied some rotational force with my fingers, it rotated the RA plate quite nicely for a single worm-and-gear hinge (that probably would not happen as well with 1.6kg extra from my camera and its counterweight sitting on top of it). All else was fine, except the hole sizes had shrunk for my standoffs, which meant that I was now manually threading 35mm of hard plastic.

I finished putting it together, but if you want to see the finished version, you'll have to look at my video demo!

VIDEO DEMO: [https://bit.ly/astrotrackerh1-demo](url)






**Total time spent: 21h** (wow that was a crazy run)

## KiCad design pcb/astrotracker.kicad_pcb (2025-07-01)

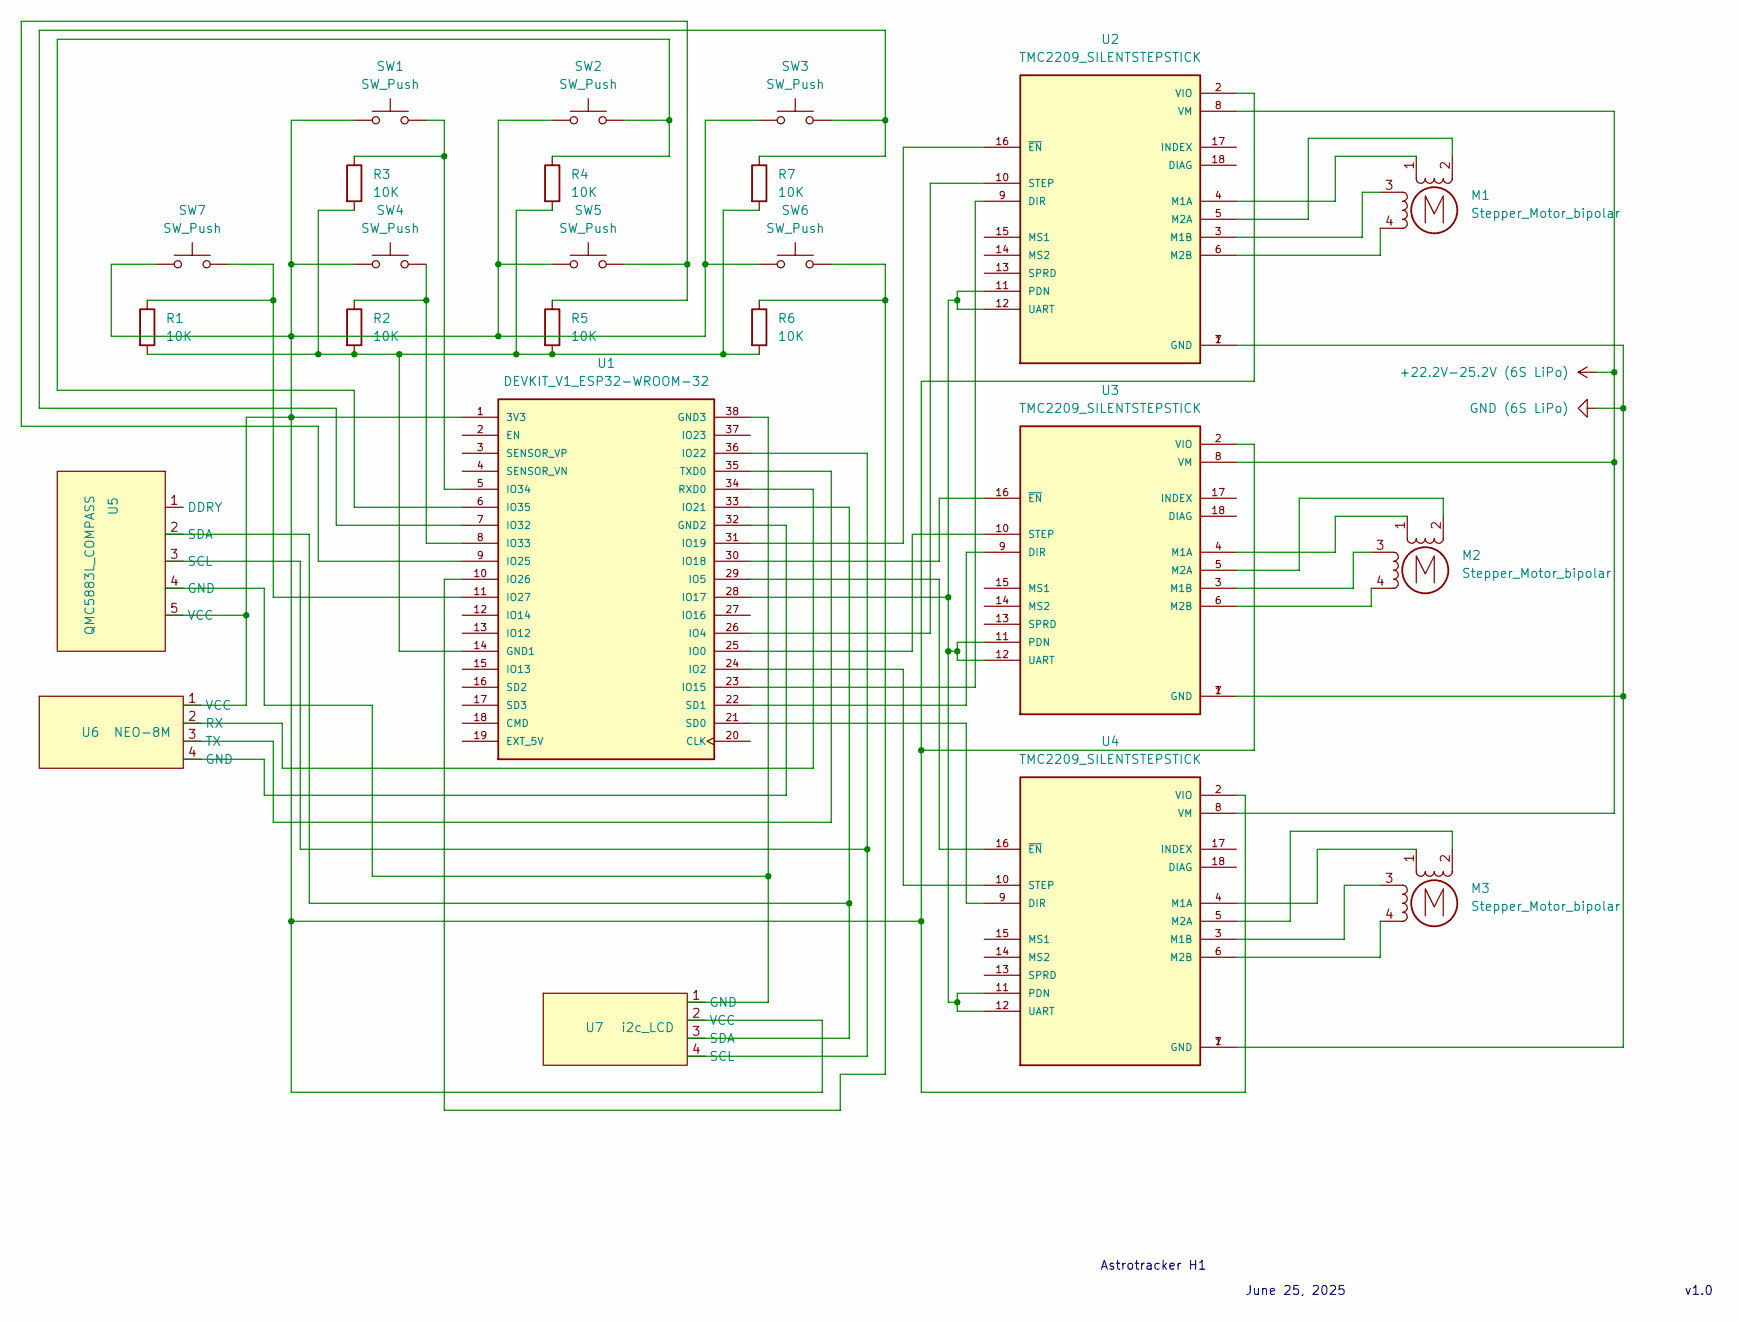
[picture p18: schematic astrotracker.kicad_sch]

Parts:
M1, M2, M3: Stepper_Motor_bipolar; NEMA-17
R1, R2, R3, R4, R5, R6, R7: 10K; R_Axial_DIN0207_L6.3mm_D2.5mm_P7.62mm_Horizontal
SW1, SW2, SW3, SW4, SW5, SW6, SW7: SW_Push; SW_PUSH_6mm
U1: DEVKIT_V1_ESP32-WROOM-32; MODULE_DEVKIT_V1_ESP32-WROOM-32; PARTREV N/A
U2, U3, U4: TMC2209_SILENTSTEPSTICK; MODULE_TMC2209_SILENTSTEPSTICK; PARTREV 1.20
U5: QMC5883L_COMPASS; QMC5883L
U6: NEO-8M; GPS NEO-8M
U7: i2c_LCD

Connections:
+22.2V-25.2V (6S LiPo): U2.8 (VM), U3.8 (VM), U4.8 (VM)
GND (6S LiPo): U2.1 (GND), U2.7 (GND), U3.1 (GND), U3.7 (GND), U4.1 (GND), U4.7 (GND)
unnamed: M1.2 (-), U2.5 (M2A)
unnamed: M2.2 (-), U3.5 (M2A)
unnamed: M3.2 (-), U4.5 (M2A)
unnamed: SW1.1, SW2.1, SW3.1, SW4.1, SW5.1, SW6.1, SW7.1, U1.1 (3V3), U2.2 (VIO), U3.2 (VIO), U4.2 (VIO), U5.5 (VCC), U6.1 (VCC), U7.2 (VCC)
unnamed: R1.2, R2.2, R3.2, R4.2, R5.2, R6.2, R7.2, U1.14 (GND1)
unnamed: U1.32 (GND2), U6.4 (GND)
unnamed: U1.38 (GND3), U5.4 (GND), U7.1 (GND)
unnamed: U1.25 (IO0), U3.10 (STEP)
unnamed: U1.24 (IO2), U4.10 (STEP)
unnamed: U1.26 (IO4), U2.10 (STEP)
unnamed: U1.29 (IO5), U4.16 (~EN)
unnamed: U1.23 (IO15), U2.9 (DIR)
unnamed: U1.28 (IO17), U2.11 (PDN), U2.12 (UART), U3.11 (PDN), U3.12 (UART), U4.11 (PDN), U4.12 (UART)
unnamed: U1.30 (IO18), U3.16 (~EN)
unnamed: U1.31 (IO19), U2.16 (~EN)
unnamed: U1.33 (IO21), U5.2 (SDA), U7.3 (SDA)
unnamed: U1.36 (IO22), U5.3 (SCL), U7.4 (SCL)
unnamed: R5.1, SW5.2, U1.9 (IO25)
unnamed: R6.1, SW6.2, U1.10 (IO26)
unnamed: R1.1, SW7.2, U1.11 (IO27)
unnamed: R7.1, SW3.2, U1.7 (IO32)
unnamed: R2.1, SW4.2, U1.8 (IO33)
unnamed: R3.1, SW1.2, U1.5 (IO34)
unnamed: R4.1, SW2.2, U1.6 (IO35)
unnamed: U1.34 (RXD0), U6.2 (RX)
unnamed: U1.21 (SD0), U4.9 (DIR)
unnamed: U1.22 (SD1), U3.9 (DIR)
unnamed: U1.35 (TXD0), U6.3 (TX)
unnamed: M1.1, U2.4 (M1A)
unnamed: M1.3, U2.3 (M1B)
unnamed: M1.4, U2.6 (M2B)
unnamed: M2.1, U3.4 (M1A)
unnamed: M2.3, U3.3 (M1B)
unnamed: M2.4, U3.6 (M2B)
unnamed: M3.1, U4.4 (M1A)
unnamed: M3.3, U4.3 (M1B)
unnamed: M3.4, U4.6 (M2B)

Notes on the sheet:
v1.0
June 25, 2025
Astrotracker H1

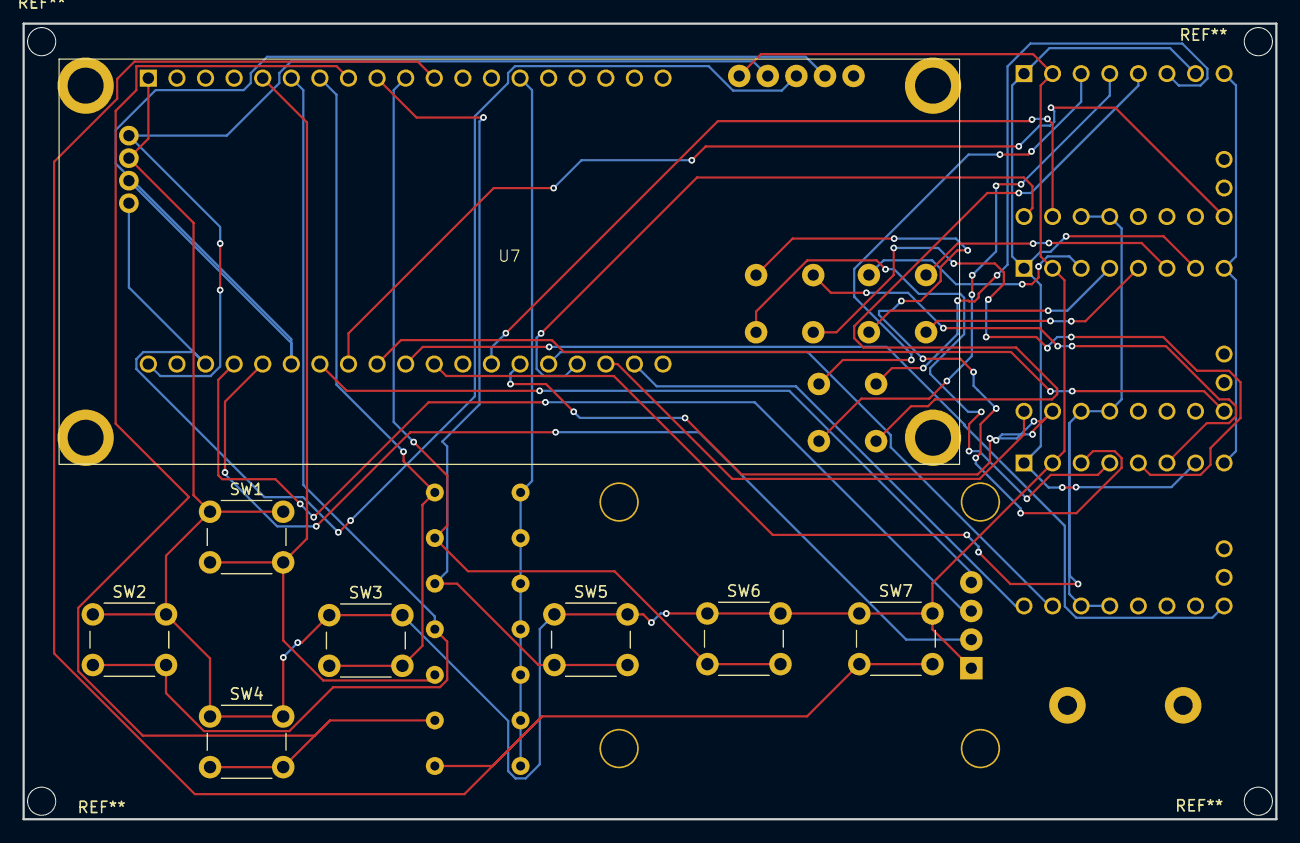
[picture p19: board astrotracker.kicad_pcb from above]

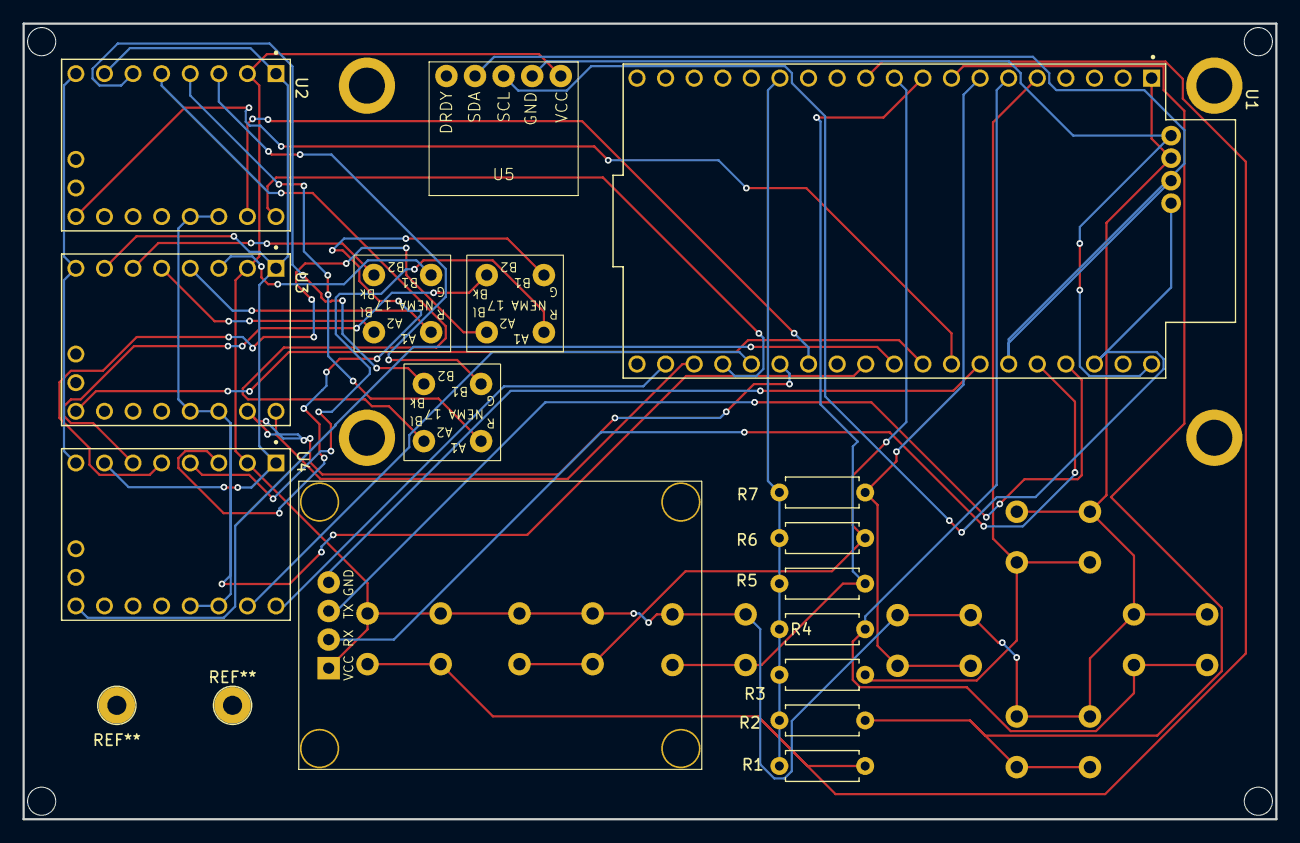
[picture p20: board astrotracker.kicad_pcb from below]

Board: 2 copper layers, 111.3 x 70.7 mm, 24 parts (16 on the bottom side), 39 nets.

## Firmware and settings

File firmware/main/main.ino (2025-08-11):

// Astrotracker H1 - a DIY star tracker for astrophotography with a 360° azimuthal axis, adjustable tilt, and automatic North Pole finding.
// Made by Jayden Leung (Hack Club Slack: @loliipoppi)
// https://github.com/jaydenaleung/astrotrackerH1

// Disclaimer: I used some of the code from various tutorial websites and library examples around the internet. This was mainly just general code such as
// starting the serial, defining library class objects, etc. that is generally required to use the library anyway. The only significant portion of code that
// was not mine is under the calibrateCompass() function which comes installed with the QMC5883LCompass Arduino library.

// NOTE: MANY QMC5883L MODULES DO NOT HAVE THE GENUINE QMC5883L CHIP, EVEN IF THEY CLAIM THEY DO. THERE ARE TWO OPTIONS FROM HERE: BUY A MAGNOMETER CHIP FROM A MORE REPUTABLE
// SELLER OR CONSIDER THAT YOUR CHIP MAY ACTUALLY BE A QMC5883P CHIP. THIS CODE IS WRITTEN FOR THE QMC5883P CHIP, SINCE THAT'S WHAT I HAVE. THE DATASHEET FOR IT IS IN THE FOLDER PATH:
// astrotrackerH1\pcb\libraries\QMC5883L\QMC5883P Datasheet Rev.C (considering that my QMC5883L is actually a QMC5883P. The footprint and schematic are the same nevertheless.)

// NOTE: THE NEMA 17 MODEL LISTED IN THE BOM'S WIRING IS OFTEN NOT AS IS SAID ON AMAZON. MY MOTOR WIRING IS: 1A/A+ = BLACK; 2A/A- = RED; 1B/B+ = GREEN; 2B/B- = BLUE.

//////////////////////////////////////////////////////////////////

// here include libraries
#include <Wire.h> // comes preinstalled on ESP32's Arduino core
#include <HardwareSerial.h> // comes preinstalled on ESP32's Arduino core
#include <Preferences.h> // comes preinstalled on ESP32's Arduino core
#include <LiquidCrystal_I2C.h> // LiquidCrystal I2C library by Frank de Brabander
#include <TinyGPSPlus.h> // TinyGPSPlus library by Mikal Hart
#include <QMC5883LCompass.h> // QMC5883LCompass library by MPrograms
#include <AccelStepper.h> // AccelStepper library

// initialize preferences
Preferences prefs;

// set serial baud rate
const long SERIAL_BAUD_RATE = 115200;
const long MOTOR_BAUD_RATE = 115200;
const long GPS_BAUD_RATE = 9600;

// here initialize objects and set up libraries
LiquidCrystal_I2C lcd(0x27, 16, 2); // confirm I2C address later
TinyGPSPlus gps;
HardwareSerial gpsSerial(2);
QMC5883LCompass compass;

// here define pins
#define GPS_RX_PIN 17 // GPS's RX pin goes to the ESP32 TX pin (17)
#define GPS_TX_PIN 16 // GPS's TX pin goes to the ESP32 RX pin (16)

// Rotational axis (RA) motor
#define RA_EN_PIN 19
#define RA_STEP_PIN 4
#define RA_DIR_PIN 25

// Angle of elevation (AOE) motor
#define AOE_EN_PIN 18
#define AOE_STEP_PIN 13
#define AOE_DIR_PIN 26

// Swivel plate (SWV) motor
#define SWV_EN_PIN 5
#define SWV_STEP_PIN 14
#define SWV_DIR_PIN 27

// some pins not used for now
#define START_PIN 35
// #define STOP_PIN 26
#define ALIGN_PIN 34
// #define UP_PIN 34
// #define DOWN_PIN 33
// #define LEFT_PIN 35
// #define RIGHT_PIN 32

AccelStepper raSD(1,RA_STEP_PIN,RA_DIR_PIN); // ra = rotational axis, SD for the stepper driver, this is for the RA stepper motor 
AccelStepper aoeSD(1,AOE_STEP_PIN,AOE_DIR_PIN); // aoe = angle of elevation, SD for the stepper driver, this is for the AOE stepper motor
AccelStepper swvSD(1,SWV_STEP_PIN,SWV_DIR_PIN); // swv = swivel plate, SD for the stepper driver, this is for the swivel plate stepper motor

bool trackingState = false;
bool aligning = false;

double latReading; // reading from GPS
double azReading; // reading from magnometer
char hemisphere = 'N'; // default northern hemisphere

int secsLeft = 0; // default 0 seconds left for aligning
double upButtonTime; // counts for how many seconds the up button was held down through watching millis()
double downButtonTime; // same but with down button
double startTime; // counted in milliseconds thru millis() at the start of tracking, to counter the time elapsed since tracking started
String formattedSecsCounter = "0h 0m 0.0s"; // formatted into hh:mm:ss.ms

const int32_t STOP_VELOCITY = 0; // defined once

/* The following is commented out for TMC2209 use */

// const int32_t RA_RUN_VELOCITY = 2; // sidereal alignment (star tracking) at 0.00417807462 deg/s (~15 arcseconds/s) with 1/64 microstepping. NEMA 17 moves at 200 steps/rev = 12800 microsteps/rev. 12.5:1 belt drive gear reduction, 12800 microsteps = 1 rev of the smaller gear = 1/12.5 rev of the bigger gear (we want this to move) = 28.8 deg of the bigger gear; 0.00014507 microsteps = 28.8 deg; 1.8569201964 microsteps/s = 0.00417807462 deg/s. Round to 2 microsteps/s with ~7.7% error.
// const int RA_MSTP = 64; // microstepping 1/64
// const uint8_t RA_RUN_CURRENT_PERCENT = 50;

// const int32_t AOE_RUN_VELOCITY = 9600; // latitudinal alignment at 18 deg/s (deg/s should be a multiple of 9) with 1/16 microstepping. NEMA 17 moves at 200 steps/rev = 3200 microsteps/rev. 60:1 worm gear reduction, 3200 microsteps = 1 rev of the worm gear = 1/60 rev of plate gear = 6 deg of latitude change; 18 deg latitude change = 9600 microsteps. 18 deg/s = 9600 microsteps/s
// const int AOE_MSTP = 16;
// const uint8_t AOE_RUN_CURRENT_PERCENT = 50;
double latAngle; // latitudinal positioning of mechanism (saved in computer, physically set at start)

// const int32_t SWV_RUN_VELOCITY = 480; // azimuthal alignment at 54 deg/s with 1/16 microstepping. NEMA 17 moves at 200 steps/rev = 3200 microsteps/rev. Only one single gear attached to motor. 3200 microsteps = 360 deg; 480 microsteps = 54 deg; 480 microsteps/s = 54 deg/s
// const int SWV_MSTP = 16;
// const uint8_t SWV_RUN_CURRENT_PERCENT = 50;
double azAngle; // azithumal positioning (heading) of mechanism

/* The following is for A4988 use */

const int RA_RUN_VELOCITY = 0.464230513; // 1/16 microstepping; sidereal alignment (star tracking) at 0.00417807462 deg/s with 1/16 microstepping. NEMA 17 moves at 200 steps/rev = 3200 microsteps/rev. 12.5:1 belt drive gear reduction, 3200 microsteps = 1 rev of the smaller gear = 1/12.5 rev of the bigger gear = 28.8 deg of the bigger gear per 3200 microsteps. Sidereal rate 0.00417807462 deg/s; 6893.12725 seconds per 3200 microsteps. 3200 microsteps/6893.12725s = 0.464230513 microsteps/s
const int AOE_RUN_VELOCITY = 2400;
const int SWV_RUN_VELOCITY = 120;

// create custom characters for LCD
byte upChar[] = { B00100, B01110, B10101, B00100, B00100, B00100, B00100, B00100 };
byte downChar[] = { B00100, B00100, B00100, B00100, B00100, B10101, B01110, B00100 };
byte leftChar[] = { B00000, B00000, B00100, B01000, B11111, B01000, B00100, B00000 };
byte rightChar[] = { B00000, B00000, B00100, B00010, B11111, B00010, B00100, B00000 };
byte hemL[] = { B00111, B01000, B10000, B11000, B10111, B10000, B01000, B00111 };
byte hemR[] = { B10000, B01000, B00100, B01100, B10100, B00100, B01000, B10000 };
byte lat[] = { B00000, B00100, B01110, B10101, B10101, B10101, B01110, B00100 };
byte az[] = { B10000, B01000, B00100, B00100, B01110, B01010, B10001, B10001 };

void setup() {
  // begin serial
  Wire.begin(); // just in case Arduino code to ESP32 needs this
  Serial.begin(SERIAL_BAUD_RATE);
  gpsSerial.begin(GPS_BAUD_RATE, SERIAL_8N1, GPS_RX_PIN, GPS_TX_PIN);
  
  // set pinmodes
  pinMode(RA_EN_PIN, OUTPUT);
  pinMode(RA_STEP_PIN, OUTPUT);
  pinMode(RA_DIR_PIN, OUTPUT);

  pinMode(AOE_EN_PIN, OUTPUT);
  pinMode(AOE_STEP_PIN, OUTPUT);
  pinMode(AOE_DIR_PIN, OUTPUT);

  pinMode(SWV_EN_PIN, OUTPUT);
  pinMode(SWV_STEP_PIN, OUTPUT);
  pinMode(SWV_DIR_PIN, OUTPUT);

  pinMode(START_PIN, INPUT);
  // pinMode(STOP_PIN, INPUT);
  pinMode(ALIGN_PIN, INPUT);
  // pinMode(UP_PIN, INPUT);
  // pinMode(DOWN_PIN, INPUT);
  // pinMode(LEFT_PIN, INPUT);
  // pinMode(RIGHT_PIN, INPUT);

  // set initial digitalWrites
  digitalWrite(RA_EN_PIN,HIGH);
  digitalWrite(AOE_EN_PIN,HIGH);
  digitalWrite(SWV_EN_PIN,HIGH);

  // stepper motor setup for TMC2209
  // raSD.setup(Serial2, MOTOR_BAUD_RATE, SERIAL_ADDRESS_RA);
  // aoeSD.setup(Serial2, MOTOR_BAUD_RATE, SERIAL_ADDRESS_AOE);
  // swvSD.setup(Serial2, MOTOR_BAUD_RATE, SERIAL_ADDRESS_SWV);

  // raSD.setRunCurrent(RA_RUN_CURRENT_PERCENT);
  // raSD.enableCoolStep();
  // raSD.setMicrostepsPerStep(RA_MSTP);
  // raSD.disable();

  // aoeSD.setHardwareEnablePin(AOE_EN_PIN);
  // aoeSD.setRunCurrent(AOE_RUN_CURRENT_PERCENT);
  // aoeSD.enableCoolStep();
  // aoeSD.setMicrostepsPerStep(AOE_MSTP);
  // aoeSD.disable();

  // swvSD.setHardwareEnablePin(SWV_EN_PIN);
  // swvSD.setRunCurrent(SWV_RUN_CURRENT_PERCENT);
  // swvSD.enableCoolStep();
  // swvSD.setMicrostepsPerStep(SWV_MSTP);
  // swvSD.disable();


  // stepper motor setup for A4988
  raSD.setMaxSpeed(10000);
  aoeSD.setMaxSpeed(10000);
  swvSD.setMaxSpeed(10000);
  
  raSD.setSpeed(0);
  aoeSD.setSpeed(0);
  swvSD.setSpeed(0);

  // get position on startup
  getPosition();
  hemisphere = determineHemisphere();

  // reset values when starting up
  prefs.begin("angles", true); // open the "angles" namespace
  latAngle = prefs.getDouble("latitude", 25.0); // retrieve the physical mechanism latitude tilt that was saved the previous time using it, default to 25.0 degrees (else the polar scope will bump into the base plate)
  prefs.end();
  azAngle = azReading;

  // initialize modules
  lcd.init();
  lcd.backlight();

  lcd.createChar(0, upChar);
  lcd.createChar(1, downChar);
  lcd.createChar(2, leftChar);
  lcd.createChar(3, rightChar);
  lcd.createChar(4, hemL);
  lcd.createChar(5, hemR);
  lcd.createChar(6, lat);
  lcd.createChar(7, az);

  // default message
  home();
  
  compass.init();
  calibrateCompass();
  /* compass.setCalibration(); SET THIS FUNCTION AFTER CALIBRATION */
}

char determineHemisphere() {
  if (latReading > 0) {
    return 'N';
  } else if (latReading < 0) {
    return 'S';
  } else {
    return 'E'; // equator
  }
}

// LCD screens/messages
void home() {
  lcd.clear();
  lcd.setCursor(0,0); // return cursor to top left corner on startup
  lcd.print("READY FOR");
  lcd.setCursor(13,0);
  lcd.write((byte)4);
  lcd.setCursor(14,0);
  lcd.write((byte)5);
  lcd.setCursor(15,0);
  lcd.print("N");
  lcd.setCursor(0,1);
  lcd.print("ALIGNMENT");
}

void align() {
  lcd.clear();
  lcd.setCursor(0,0);
  lcd.print("ALIGNING");
  lcd.setCursor(9,0);
  lcd.write((byte)6);
  lcd.setCursor(10,0);
  lcd.print(latReading >= 10.0 ? round(latReading*10.0)/10.0 : round(latReading*100.0)/100.0); // round to 1 decimal place if the latitude is >= to 10, 2 if not. e.g. 42.3, 9.87. i.e. 3 sig figs.
  lcd.setCursor(14,0);
  lcd.write((byte)7);
  lcd.setCursor(15,0);
  lcd.write(hemisphere);
  lcd.setCursor(0,1);
  lcd.print(secsLeft);
  lcd.setCursor(0,3);
  lcd.print("secs left...");
}

void alignComplete() {
  lcd.clear();
  lcd.setCursor(0,0);
  lcd.print("ALIGN COMPLETE");
  delay(1000);
}

void up() {
  if (aligning == false && trackingState == false) {
    lcd.setCursor(15,1);
    lcd.write((byte)0);
  }
}

void down() {
  if (aligning == false && trackingState == false) {
    lcd.setCursor(15,1);
    lcd.write((byte)1);
  }
}

void left() {
  if (aligning == false && trackingState == false) {
    lcd.setCursor(15,1);
    lcd.write((byte)2);
  }
}

void right() {
  if (aligning == false && trackingState == false) {
    lcd.setCursor(15,1);
    lcd.write((byte)3);
  }
}

void track() {
  lcd.clear();
  lcd.setCursor(0,0);
  lcd.print("TRACKING...");
  lcd.setCursor(0,1);
  lcd.print(formattedSecsCounter);
}

void count() {
  lcd.setCursor(0,1);
  lcd.print(formattedSecsCounter);
}

void trackStopped() {
  lcd.clear();
  lcd.setCursor(0,0);
  lcd.print("STOPPED");
  delay(1000);
}

void loop() {
  
  // if (hemisphere == 'N' || hemisphere == 'E') {
  //   raSD.enableInverseMotorDirection(); // counterclockwise - rotate this way for tracking in Northern Hemisphere
  // } else {
  //   raSD.disableInverseMotorDirection(); // clockwise - Southern Hemisphere
  // }

  getPosition();

  // button logic
  if (digitalRead(START_PIN) == LOW && trackingState == false) { // button pressed to start
    trackingState = true;
    startTime = (double)(millis()); // must convert millis() to double because it returns as an unsigned long (integer)
    track(); // update LCD
    trackingStart();
  }

  if (trackingState == true && digitalRead(START_PIN) == HIGH && digitalRead(STOP_PIN) == HIGH) { // during tracking
    formattedSecsCounter = updateCount();
    count();
  }

  if (digitalRead(STOP_PIN) == LOW && trackingState == true) { // button pressed to start
    trackingStop();
    trackStopped(); // update LCD
    trackingState = false;
  }

  if (digitalRead(ALIGN_PIN) == LOW && aligning == false) {
    aligning = true;
    secsLeft = round(((latReading / 18) * 1000) + ((azAngle / 54) * 1000)); // calculate remaining seconds
    align(); // update LCD
    latitudeAlign(); // align latitudinally
    secsLeft = round((azAngle / 54) * 1000); // calculate remaining seconds - latiudinal alignment seconds
    align(); // update LCD
    azithumalAlign(); // align azithumally
    alignComplete(); // update LCD
    aligning = false;
  }

  if (digitalRead(UP_PIN) == LOW) {
    aoeSD.enable();
    if (trackingState == true) {trackingState = false;} // stop tracking // no conditions for azimuthal and latitudinal auto-aligning because they have the program-pausing function .delay()
    aoeSD.enableInverseMotorDirection(); // counterclockwise = latitude up
    aoeSD.moveAtVelocity(AOE_RUN_VELOCITY);
  } else {
    aoeSD.disable();
    latAngle += ((double)(millis()) - upButtonTime) * 18; // get the time that the button was pressed for and convert it to degrees
    saveMechLat();
  }
  if (digitalRead(UP_PIN) == HIGH) { // crucial that this code is after and seperate from the else block, so that upButtonTime doesn't reset before it updates latAngle
    upButtonTime = (double)(millis());
  }

  if (digitalRead(DOWN_PIN) == LOW) {
    aoeSD.enable();
    if (trackingState == true) {trackingState = false;}
    aoeSD.disableInverseMotorDirection(); // clockwise = latitude down
    aoeSD.moveAtVelocity(AOE_RUN_VELOCITY);
  } else {
    aoeSD.disable();
    latAngle -= ((double)(millis()) - downButtonTime) * 18;
    saveMechLat();
  }
  if (digitalRead(DOWN_PIN) == HIGH) {
    downButtonTime = (double)(millis());
  }

  if (digitalRead(LEFT_PIN) == LOW) {
    swvSD.enable();
    if (trackingState == true) {trackingState = false;}
    swvSD.enableInverseMotorDirection(); // counterclockwise = left
    swvSD.moveAtVelocity(AOE_RUN_VELOCITY);
  } else {
    swvSD.disable();
  }

  if (digitalRead(RIGHT_PIN) == LOW) {
    swvSD.enable();
    if (trackingState == true) {trackingState = false;}
    swvSD.disableInverseMotorDirection(); // clockwise = right
    swvSD.moveAtVelocity(AOE_RUN_VELOCITY);
  } else {
    swvSD.disable();
  }
}

void saveMechLat() {
  prefs.begin("angles", false); // open a namespace in the ESP32 non-volatile memory
  prefs.putDouble("latitude", latAngle); // save the latAngle in long-term memory
  prefs.end();
}

void calibrateCompass() { // DISCLAIMER: THIS CODE SECTION IS NOT MINE. I TOOK IT FROM THE GIVEN "EXAMPLES" SECTION OF THE ARDUINO LIBRARY I USED (QMC5883LCompass.h library by MPrograms). I TAKE NO CREDIT FOR THE CODE WITHIN THIS FUNCTION.
  Serial.println("This will provide calibration settings for your QMC5883L chip. When prompted, move the magnetometer in all directions until the calibration is complete.");
  Serial.println("Calibration will begin in 5 seconds.");
  delay(5000);

  Serial.println("CALIBRATING. Keep moving your sensor...");
  compass.calibrate();

  Serial.println("DONE. Copy the lines below and paste it into your projects sketch.);");
  Serial.println();
  Serial.print("compass.setCalibrationOffsets(");
  Serial.print(compass.getCalibrationOffset(0));
  Serial.print(", ");
  Serial.print(compass.getCalibrationOffset(1));
  Serial.print(", ");
  Serial.print(compass.getCalibrationOffset(2));
  Serial.println(");");
  Serial.print("compass.setCalibrationScales(");
  Serial.print(compass.getCalibrationScale(0));
  Serial.print(", ");
  Serial.print(compass.getCalibrationScale(1));
  Serial.print(", ");
  Serial.print(compass.getCalibrationScale(2));
  Serial.println(");");
}

void getPosition() { // setup the GPS and magnometer
  // get latitude from GPS
  while (gpsSerial.available() > 0) {
    char gpsData = gpsSerial.read(); // get raw data
    Serial.println(gpsData);
    gps.encode(gpsSerial.read()); // encode into readable format
  }
  if (gps.location.isUpdated()) {
    latReading = gps.location.lat(); // get latitude
  }

  // get heading from magnometer
  compass.read(); // get compass data
  azReading = compass.getAzimuth(); // take the heading data from the compass and assign it to azReading
}

String updateCount() {
  double milsec = (double)(millis()) - startTime;;
  double seconds = milsec / 1000.0; // convert forward all the way to exact number of hours
  milsec = 0;
  double minutes = seconds / 60.0;
  seconds = 0;
  double hours = minutes / 60.0;
  minutes = 0;
  
  minutes = (hours-(double)((int)hours)) * 60.0; // convert exact number of hours into readable hh:mm:ss.ms format
  hours = (int)hours; // correct the hours by only displaying the remainder after 24 hours has been converted into and shown as a day
  seconds = (minutes-(double)((int)minutes)) * 60.0; // now truncate the decimals from days since that remainder time has been transferred to hours 
  minutes = (int)minutes; // does this by truncating the higher order unit (e.g. days is higher than hours) and subtracting it from the original to get the decimal point
  milsec = (seconds-(double)((int)seconds)) * 1000.0; // then it takes that and multiplies it by its respective conversion factor to get to a lower order unit (e.g. hours to minutes)
  seconds = (int)seconds; // keeps it as a double for precision before converting it to a more readable int and String later
  milsec = (int)milsec; // truncate the milliseconds too to make it readable and to fix any accidental decimals that show up in conversion

  return (String)hours + "h " + (String)minutes + "m " + (String)seconds + "." + (String)milsec + "s" // max characters is 16, OK unless hour count goes over 100 (unrealistic)
}

void trackingStart() { // RA motor
  digitalWrite(RA_EN_PIN,LOW);
  raSD.setSpeed(RA_RUN_VELOCITY);
}

void trackingStop() { // RA motor
  raSD.setSpeed(STOP_VELOCITY); // stop
  digitalWrite(RA_EN_PIN,HIGH);
}

void latitudeAlign() { // AOE motor - 9600 microsteps per second = 18 degrees per second (60:1 worm gear reduction)
  digitalWrite(AOE_EN_PIN,LOW);
  
  if (latReading > latAngle) { // 'angle' is the goal latitude
    AOE_RUN_VELOCITY *= -1; // counterclockwise - turning the worm gear this way increases the latitudinal angle
  } else {
    // do nothing = clockwise - turning the worm gear this way decreases the latitudinal angle
  }
  
  const float duration = (latReading / 18)
  aoeSD.setSpeed(AOE_RUN_VELOCITY);
  aoeSD.move((int)(duration*AOE_RUN_VELOCITY));
  aoeSD.setSpeed(STOP_VELOCITY); // stop

  if (latReading > latAngle) { // change it back
    AOE_RUN_VELOCITY *= -1;
  }
  
  latAngle = latReading;
  saveMechLat();

  digitalWrite(AOE_EN_PIN,HIGH);
}

void azimuthalAlign() { // swivel motor - 480 microsteps per second = 54 degrees per second
  digitalWrite(SWV_EN_PIN,LOW);

  if (azAngle < 180 || azAngle = 180) { // 0 deg is the goal heading, direction depends on mechanism heading given by magnometer
    SWV_RUN_VELOCITY *= -1; // counterclockwise - turning the mechanism towards North
    const int duration = (azAngle / 54) * 1000; // in milliseconds
  } else {
    // do nothing - clockwise - turning the mechanism towards North
    const int tempAngle = azAngle - 180;
    const int duration = (tempAngle / 54) * 1000;
  }
  
  swvSD.setSpeed(SWV_RUN_VELOCITY);
  aoeSD.move((int)(duration*SWV_RUN_VELOCITY));
  swvSD.setSpeed(STOP_VELOCITY); // stop

  if (azAngle < 180 || azAngle = 180) {
    SWV_RUN_VELOCITY *= -1; // turn it back
  }

  digitalWrite(SWV_EN_PIN,HIGH);
  secsLeft = 0; // reset after alignment is finished
}

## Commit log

2025-06-25 pcb design
    [astrotracker.kicad_sch]
2025-06-25 update pcb libraries
    [TMC2209_SILENTSTEPSTICK.step]
2025-06-25 finish pcb
    [astrotracker.kicad_pcb, astrotracker.kicad_sch]
2025-06-25 commit pcb
2025-06-29 FINISH PCB CAD
    [astrotracker.kicad_pcb, astrotracker.step]
2025-06-30 complete cad folder
    [M2.5x10mm spacer.step, M2.5x9.6mm spacer.step, M3x8mm spacer.step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]
2025-07-01 final (hopefully)
    [BOM.csv, astrotracker.kicad_pcb]
2025-07-01 organization + final commit!! before submitting
    [astrotracker.kicad_pcb, astrotracker.kicad_sch]
2025-07-01 last commit
    [astrotracker.kicad_pcb, astrotracker.kicad_sch]
2025-07-07 update gerbers
2025-07-16 update cad
    [M2.5x10mm spacer.step, M2.5x9.6mm spacer.step, M3x8mm spacer.step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]
2025-07-16 cad upadte
    [Swivel Plate - Part 1.stl, Swivel Plate - Part 4.stl, Swivel Plate - Part 6.stl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]
2025-07-16 added gcodes
    [EN4PRO_RA Plate - Part 1.3mf, EN4PRO_Swivel Plate - Part 4.3mf, EN4PRO_Swivel Plate - Part 7.3mf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]
2025-08-04 add schematic to readme
